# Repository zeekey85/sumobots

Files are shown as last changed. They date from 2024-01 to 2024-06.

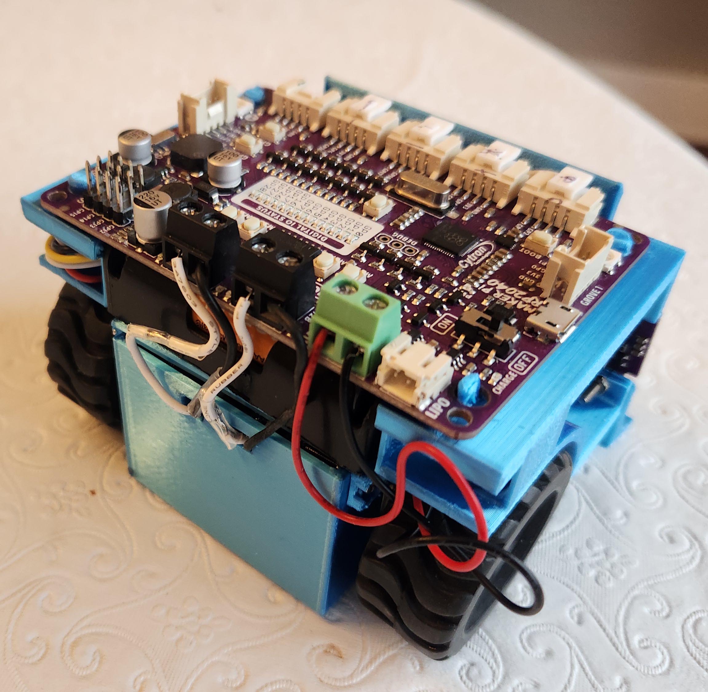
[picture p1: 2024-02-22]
Builders/Bill Ball/Sumo 8/Complete views/sumo 8 back.jpg

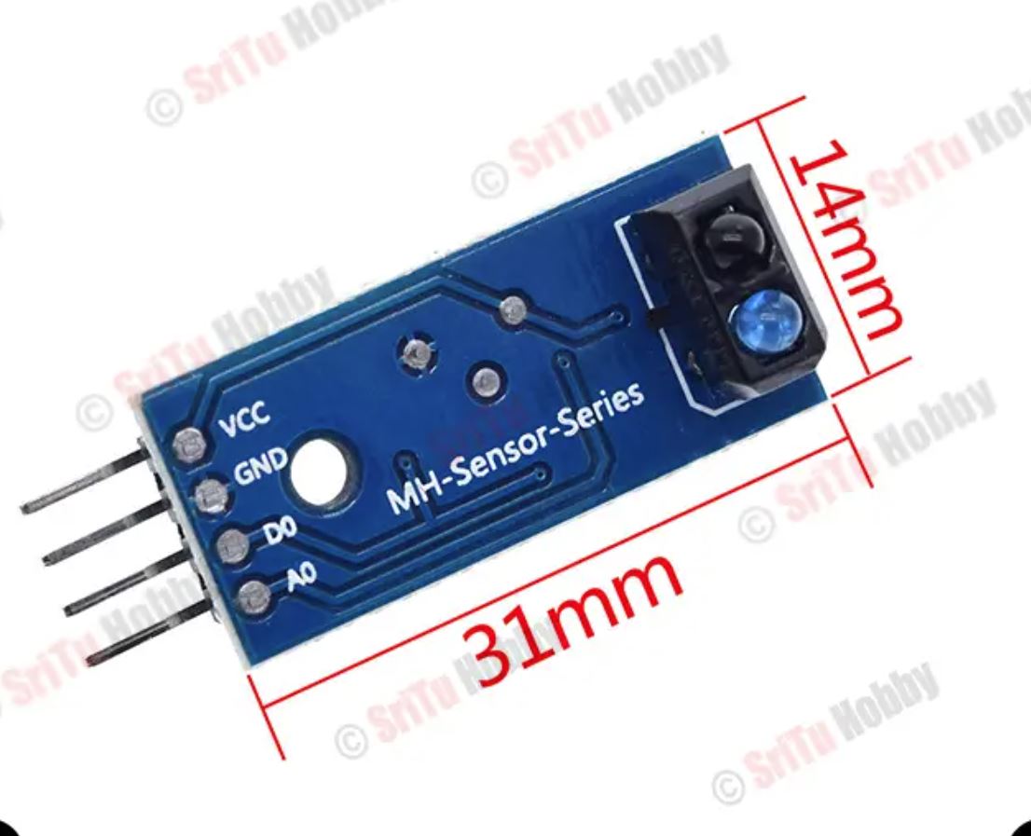
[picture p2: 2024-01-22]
reference/design files/Measurements and images/TCRT5000 measurements.JPG

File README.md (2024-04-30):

# sumobots
A place for development documents and public relases on the mini sumo bot project from It Begins in Brockport.  
Here your will find everything you need to build and compete with your own IBIB2040 class mini sumo bot in the Released folder of this archive.  
General information can be found at https://ibib.us/projects/mini-sumo-robots/  
Contact Bill Ball, bill@tinkerfarm.net with any questions.

Sumo Louis

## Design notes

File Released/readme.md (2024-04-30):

These files are released for public use as a starting point for builds of the IBIB2040 class of Mini Sumo Bots.
A rules document for competition is included.  
An example build is provided in the designs/BB1 folder. This includes a parts list and preparation document, an assembly document, and 3D printable files to create a chassis. A limited number of kits from this build are available.  
Software to be downloaded to the Maker PI2040 board can be found in the code folder.  
General information about the project can be found at https://ibib.us/projects/mini-sumo-robots/  
Send all inquries to Bill at bill@tinkerfarm.net.  

two

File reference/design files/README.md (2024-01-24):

# sumobots
Schematics and datasheets for building and programming IBiB mini sumo bots
Contact Bill Ball, bill@tinkerfarm.net with any questions.

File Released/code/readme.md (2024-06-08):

# Sumo Bot

## Initial setup
Open `settings.py` and review the "Robot hardware settings" section. Change any pin values if your hardware is connected differently than the default settings.

## Installation instructions
Make a backup copy of the code.py file that cam on your MakerPi board.
Copy the files `base-bot.py`, `code.py`, `adafruit_vl53l0x.mpy`, and `settings.py` to your MakerPi to get a working sumo bot.

## How to use
Turn on your MakerPi. To start a bout hold down the GP20 button until the light turns yellow. Your bot is now armed. Release the button to start the bout after a 5 second delay.
See the rules document for more detail on how Sumo bot matches operate.
Turn on your Maker Pi and press buttons until you find the one that turns the lights from red to yellow. Your bot is now armed. Release the button to enter FIGHT MODE!

## How to customize
Change values in the "Settings that control fight mode parameters" section of `settings.py` to make adjustments to your robot's fighting strategy.

## Advanced customization
Modify the `fight()` method in code.py to change your robot's fighting strategy.

## File descriptions 
* `settings.py` contains hardware pin assignments and basic behavior settings
* `code.py` defines the `fight()` method which determines the robot's logic while in fight mode.
* `base_bot.py` contains the main class which defines the fundamental methods for robot control such as moving and detecting enemies.
* `adafruit_Vl530x.mpy` is the driver for the time of flight sensors. The robot code won't work without it installed on the MakerPi.
* `original_code.py` is the default demo program that shipped with the MakerPI RP2040. It's not needed for the robot to work.

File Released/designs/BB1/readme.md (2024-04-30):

This is the complete plans for a mini sumo robot that conforms to IBiB2040 rules and is based around the Maker Pi RP2040 robotics board. It also comples with the generally used mini sumo rules.

An illustrated complete parts list is included in the "parts preparation.pdf" document.

Stl files for 3D printing the four body parts are included.

Illustrated assembly instructions can be found in the "assembly instructions.pdf" file.

The Maker Pi board should be running CircuitPython (it ships this way) and will need the code files in the code folder copied to it.

All material in this archive except the adafruit_vl53l0x.py file is CC0 "no rights reserved." adafruit_vl53l0x.py has a MIT license.  
Send any questions to: bill@tinkerfam.net

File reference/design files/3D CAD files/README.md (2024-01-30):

# sumobots
CAD files to be used to design IBiB mini sumo bots.
Contact Bill Ball, bill@tinkerfarm.net with any questions.

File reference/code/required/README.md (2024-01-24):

# sumobots
Reference code to include in sumo bots.

original code.py is the defaut code shipped on Maker pi boards. It should be included on all sumo boards.

adafruit_vl530x.mpy is the driver for the ranging sensors. It should be included in the lib folder of all sumo boards.

The Adafruit repository for CircuitPython on the maker pi board is here: https://circuitpython.org/board/cytron_maker_pi_rp2040/
The board ships with CircuitPython 7.1.0

Contact Bill Ball, bill@tinkerfarm.net with any questions.

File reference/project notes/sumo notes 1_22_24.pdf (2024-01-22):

IBiB Mini Sumo project notes. 1/21/2024. Bill Ball

The bots will meet standard specifications: 10cm x 10cm x unlimited, 500 grams max.

The bots will have the following components:

1. 4xaa battery holder. $0.5-$1. Is the 1x4 or 2x2 layout better? Builders supply their own batteries.

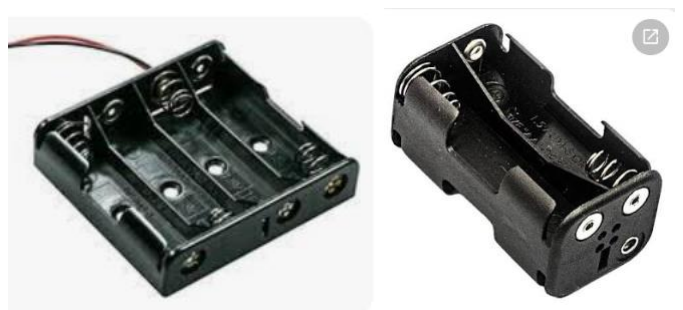
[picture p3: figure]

2. Maker Pi RP2040 main board with OEM Circuitpython 7 and accompanying 4 x grove to header pin wire sets. Cheapest source in bulk @$10: Newark. Manufacturer reference: https://www.cytron.io/p-maker-pi-rp2040-simplifying-robotics-with-raspberry-pi-rp2040 (https://www.cytron.io/p-maker-pi-rp2040-simplifying-robotics-with-raspberry-pi-rp2040)

The adafruit_vl5310x.mpy library will be installed by us. The default code.py will be renamed and a basic sumo bot program will be added as code.py.

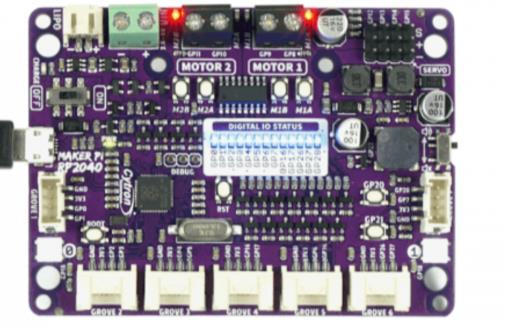
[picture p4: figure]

3. N20 6V motors (2). What rpm/torque trade off is best? We will start at 150rpm. $4.20 per pair from Aliexpress. We will need to solder on leads. Mounting brackets will be 3D printed (standard ones are too short for the wheels).

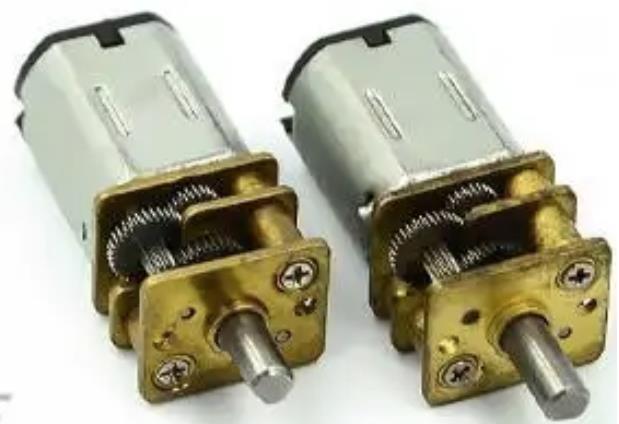
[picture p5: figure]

### 4. K346 43*19*3mm D-hole Rubber Wheel (2). $1.5 per pair from Aliexpress

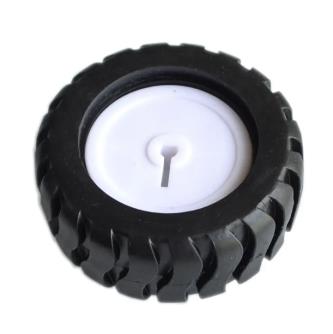
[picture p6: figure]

5. VL53L0X Time-of-Flight Ranging Sensor (2). $2.60 per pair from Aliexpress. We will need solder the header pins. We will use the VCC, GND, SCL, SDA, and XSHUT pins. XSHUT is required to change the I2C address in software. We are not planning to use the GPI01 (data ready) pin (it would require an additional grove wire set if we do). If two sensors doesn’t work well we may need to go to three, which would require 2 additional grove wire sets and may not all fit on the same I2C bus as exposed by the Maker pi.

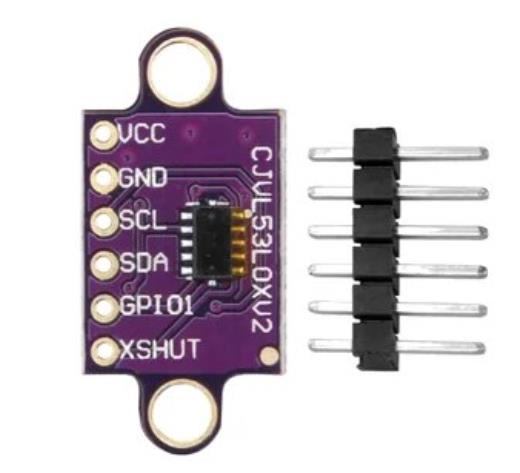
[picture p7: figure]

6. TCRT5000 Infrared Reflective Sensor Module (2). $1.5 per pair from Aliexpress.

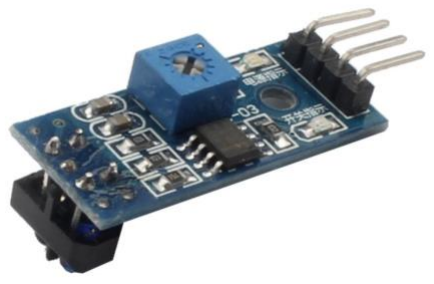
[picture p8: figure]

7. USB A to micro USB cable for programing. We may want to offer other formats to micro options. $1 from Aliexpress. People don’t otherwise acquire micro USB cables anymore.
8. Chassis. etc. The chassis can be user designed/built. We will need to develop a design for 3D printing, maybe laser cut or even milled. We also need to decide on ballast and fasteners. The basic bot only weighs about 250 grams. We should supply enough repositionable ballast to reach 500 grams. I use steel BBs but they need to be contained. We can do this project with m2 Philips head fasteners throughout. It would be incredibly kind to builders if fasteners are all the same length. 14mm? As a supplied kit let’s plan on $5 total cost of supplies.

Total delivered cost is currently about $27 for supplies when items are purchase qty 10 or greater using mostly Aliexpress.

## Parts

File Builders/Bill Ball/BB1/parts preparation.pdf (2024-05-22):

Parts preparation information for the Mini Sumo BB1 robot.

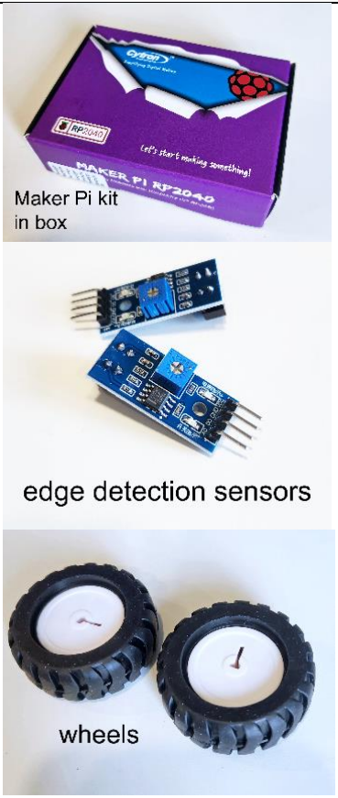
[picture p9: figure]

1. The parts list for the robot:

A Maker Pi RP2040 kit in box. The box includes one Maker Pi board, 4 Grove connector to female header pin cables, a mini screwdriver, and 4 adhesive feet. The feet are not used in this project.

Two ToF (VL53L0X Time of Flight) sensors of the type pictured in this document.

Two edge detection (TCRT5000 infrared reflective) sensors of the type pictured in this document (with right angle header pins, sensor and adjustment screw on opposite sides).

Two N20 6 volt gear head motors, low torque models only. 150 or 200 rpm motors suggested.

Wire and heat shrink for motor leads if they are not pre-soldered to the motors.

Two 43mm x 19mm treaded tires mounted on 3mm D shaft wheels, as shown.

One 4 x AA battery holder of the type pictured in this document, along with 4 AA batteries.

A minimum of eight m3 x 10mm pan head screws (referred to as bolts in the documentation).

One m3 x 10mm countersunk screw (referred to as bolts in the documentation).

A minimum of 9 nuts for the m3 bolts.

Four 3D printed parts.

Ballast weight as desired. About 200 grams of Steel BBs are suggested.

A Phillips screwdriver.

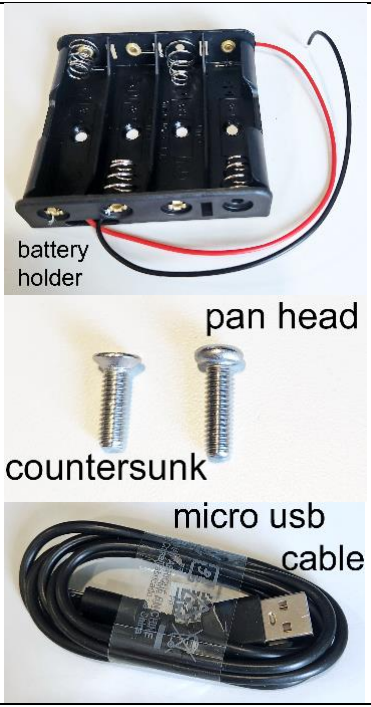
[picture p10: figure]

Small needle-nosed pliers.

A micro USB cable for programming, along with downloaded software.

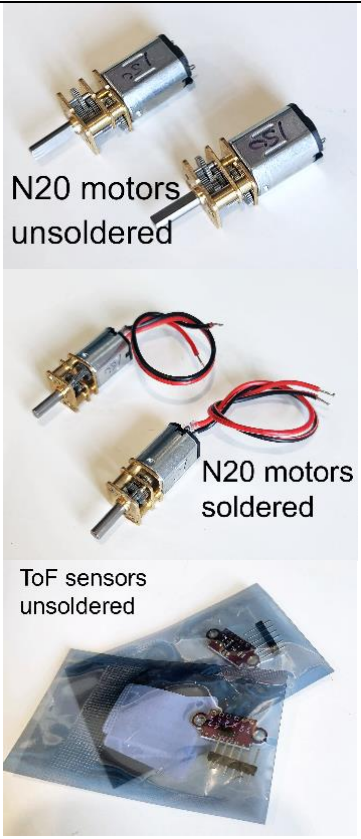
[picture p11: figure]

2. If the motor wires are not soldered to the motors and this exposed wire at the connection covered with heat shrink, this will need to be done with two pairs of wire, about 80mm long.

The edge detection sensors usually ship with right angle header pins already soldered on and in anti-static bags. They do not need further preparation.

The ToF sensors usually ship unsoldered with header pins included in the anti-static bag.

The yellow protective film covering the black rectangle on the ToF sensors will need to be removed if it has not already been done.

If the ToF sensors have not had their header pins soldered on, this will need to be done. The longer pins are in the back of the sensor and it is soldered from the front.

3. The four 3D printed parts: main body, fender bar, lid, and blade can be printed with standard settings. Printing time varies widely but plan on 8 hours of print time total.

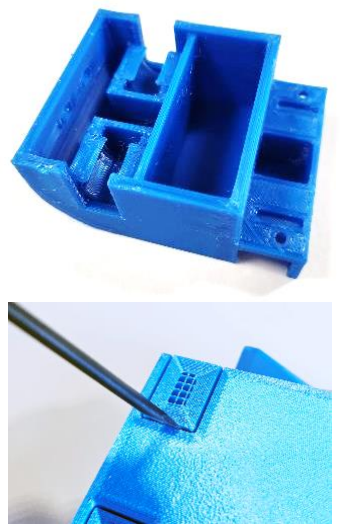
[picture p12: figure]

Only the main body needs to be printed with supports. The body is printed upright on the printer bed, as shown. Once it is off the printer the supports can be removed by popping them off the side of the body and at the curved rear from underneath. The supports interface to the main body does not need to be cleaned up fully, although the bolt holes should be cleared.

The fender bar is printed “face” down on the bed, as shown.

The lid should be printed upside down on the bed, as shown, with the flat side on the bed.

The blade is printed with its back (the flattest part) on the bed, as shown. It does not need supports.

Some holes may need to be cleared with a 3mm drill bit to accommodate bolts without breaking the part.

Parts preparation is complete and assembly can begin.

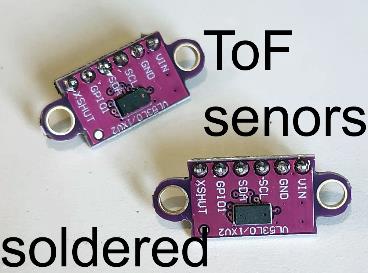
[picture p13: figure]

# Main Body

# Fender Bar

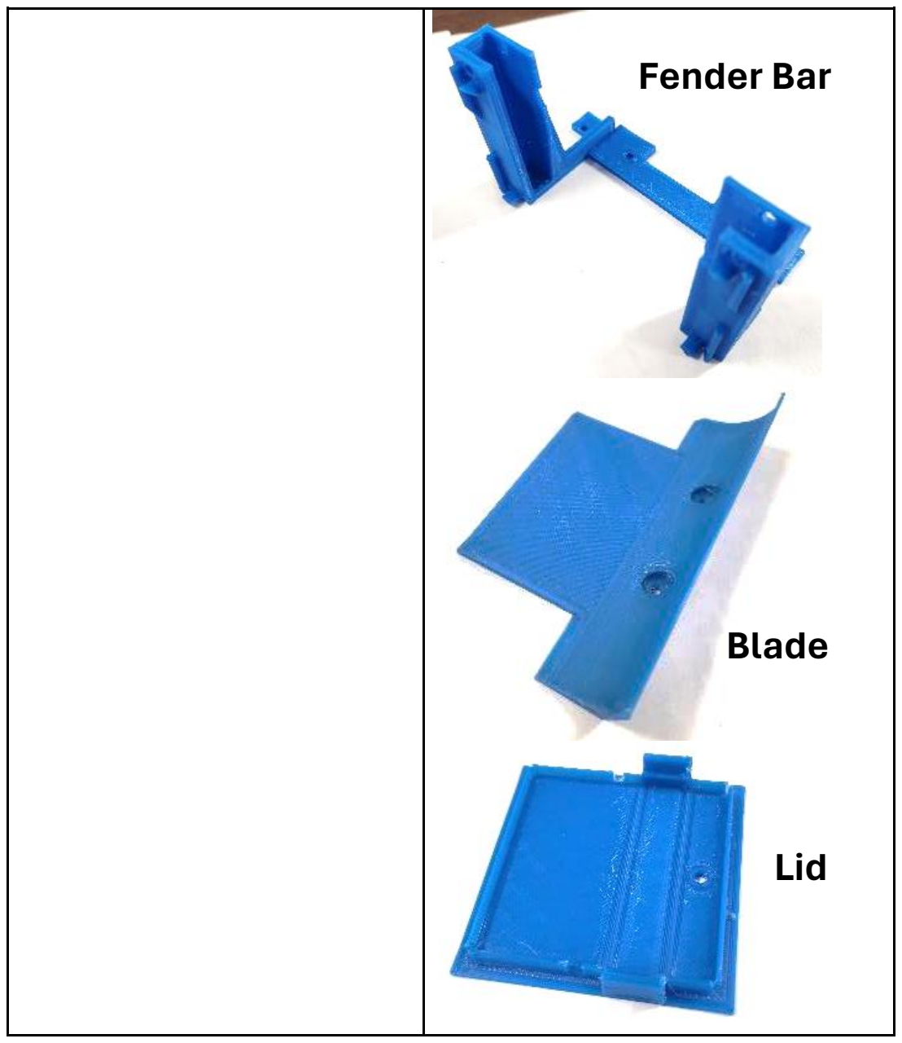
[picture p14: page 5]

# Blade

# Lid

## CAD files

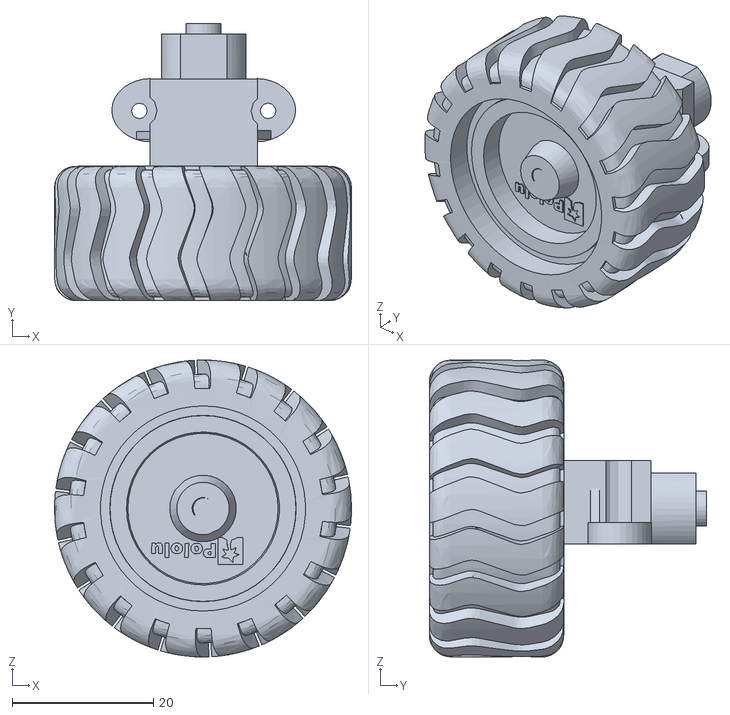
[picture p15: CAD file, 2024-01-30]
reference/design files/3D CAD files/wheelmotormount assembly.stl
42.0 x 39.2 x 42.0

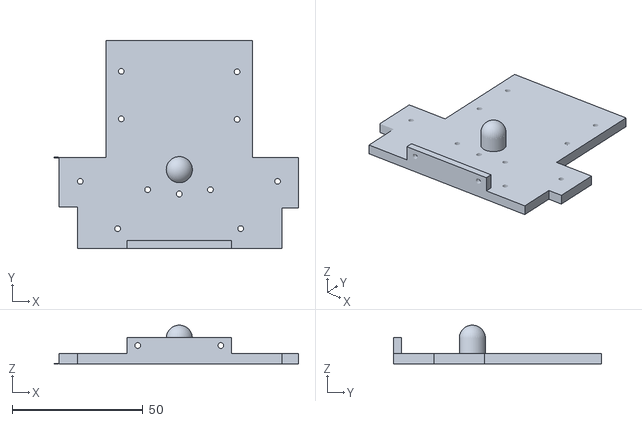
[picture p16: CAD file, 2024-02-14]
Builders/Bill Ball/Sumo 4/Files for 3D printing/main plate.stl
93.3 x 79.6 x 14.8

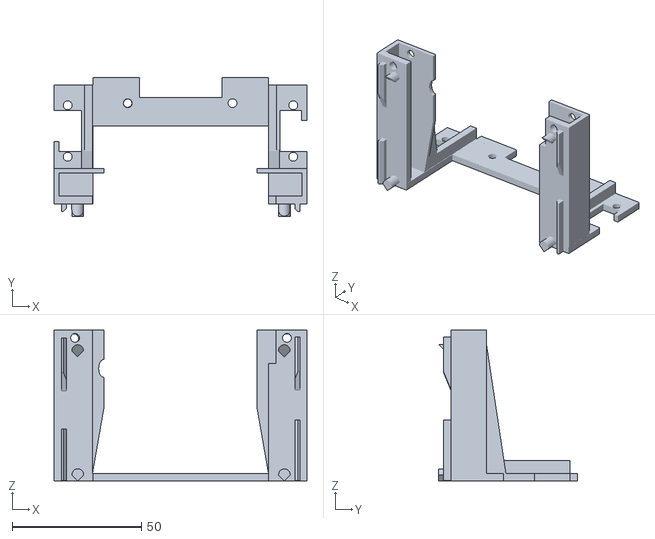
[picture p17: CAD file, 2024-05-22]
Builders/Bill Ball/BB1/Sumo BB1 fender bar.stl
97.9 x 53.9 x 58.4

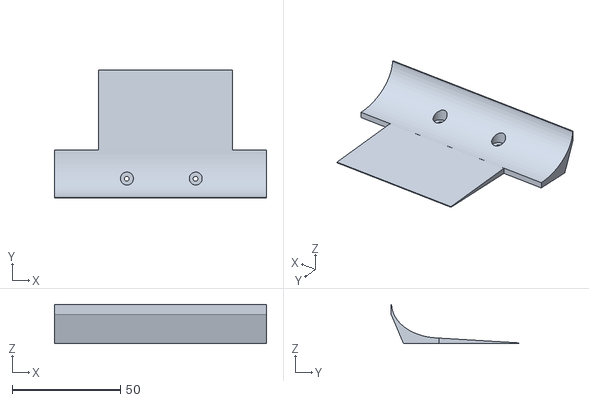
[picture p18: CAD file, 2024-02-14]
Builders/Bill Ball/Sumo 4/Files for 3D printing/blade.stl
98.0 x 59.0 x 18.1

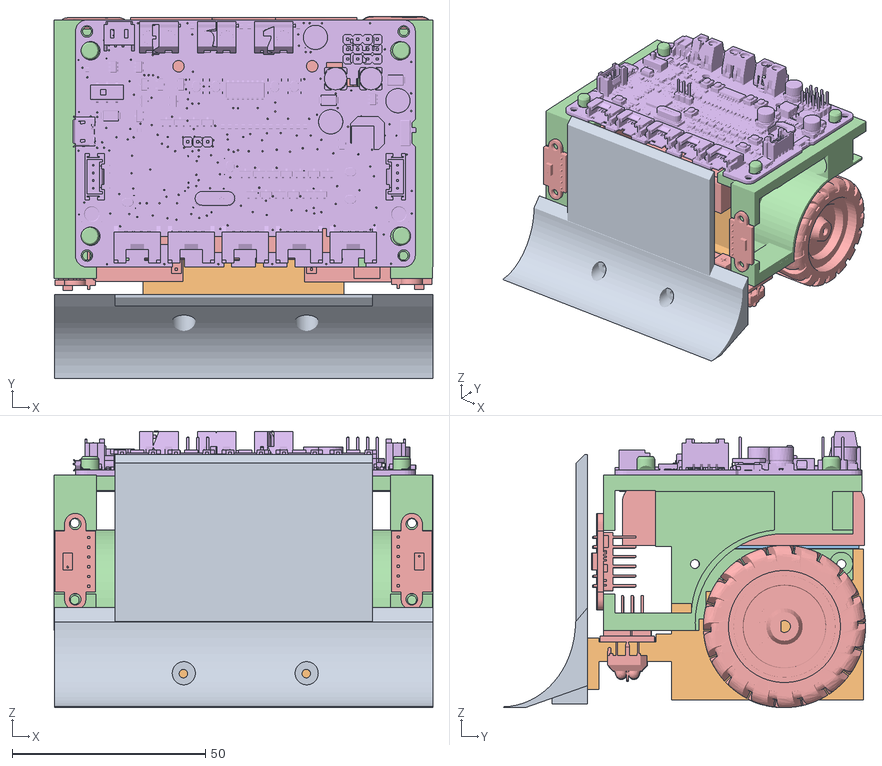
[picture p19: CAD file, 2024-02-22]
Builders/Bill Ball/Sumo 8/Complete views/tinker.obj
98.1 x 93.7 x 71.5

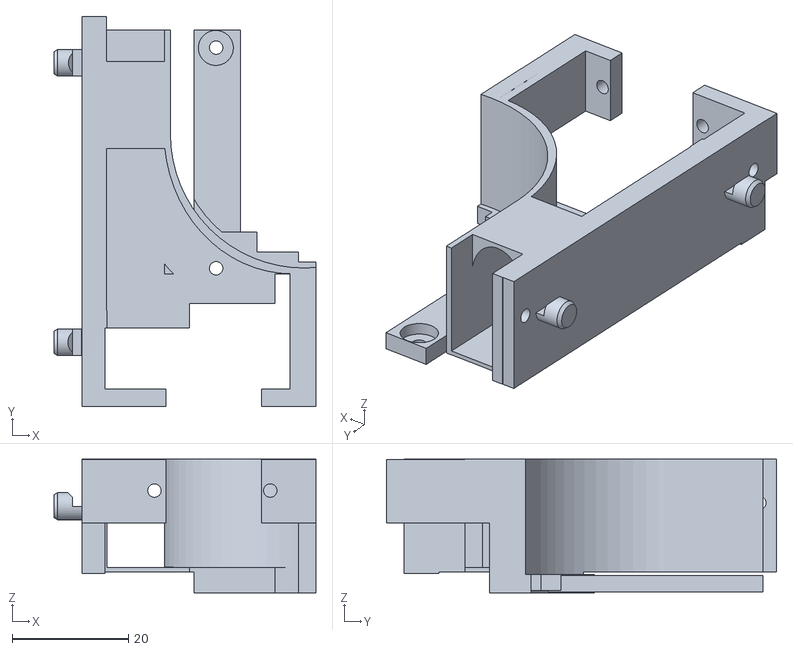
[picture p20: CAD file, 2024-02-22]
Builders/Bill Ball/Sumo 8/Parts/sumo 8 left fender.stl
45.0 x 67.0 x 22.9

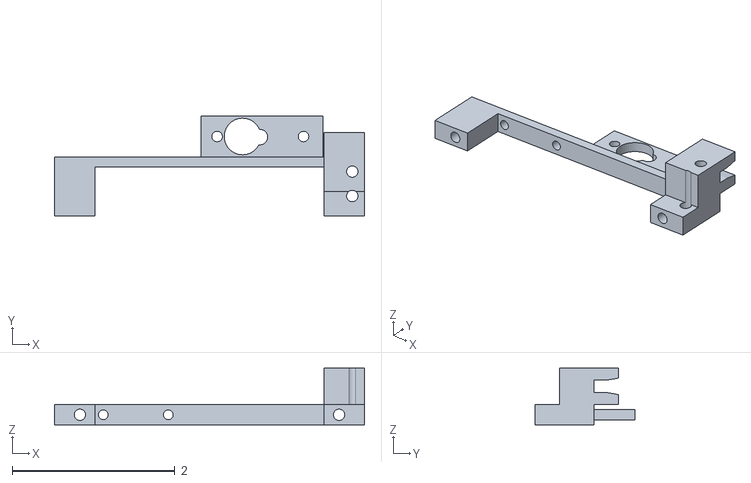
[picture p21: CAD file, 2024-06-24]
SumoBot Accessory Holder v1 v3.stl
3.81 x 1.23 x 0.7

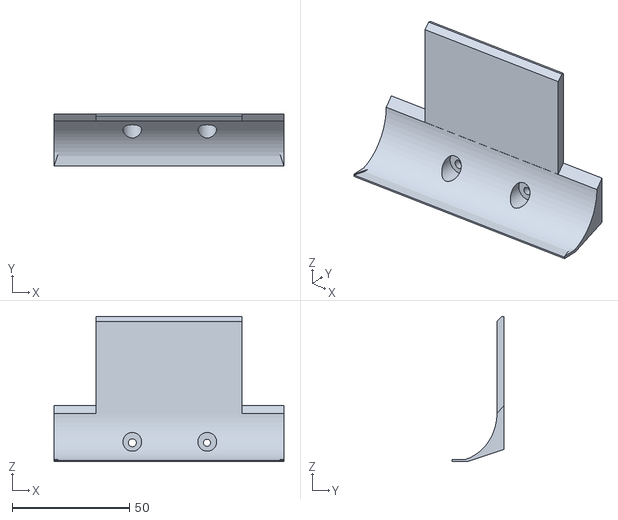
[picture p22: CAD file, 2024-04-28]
Builders/Bill Ball/BB1/Sumo BB1 blade.stl
98.0 x 22.2 x 62.0

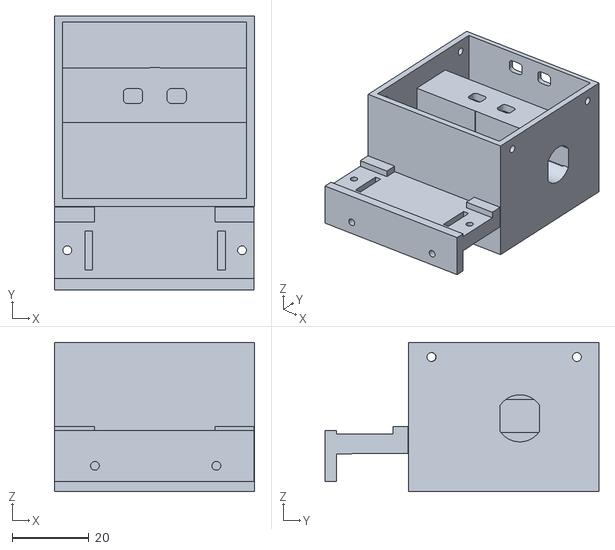
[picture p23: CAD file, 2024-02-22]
Builders/Bill Ball/Sumo 8/Parts/sumo 8 body.stl
52.2 x 71.5 x 39.0

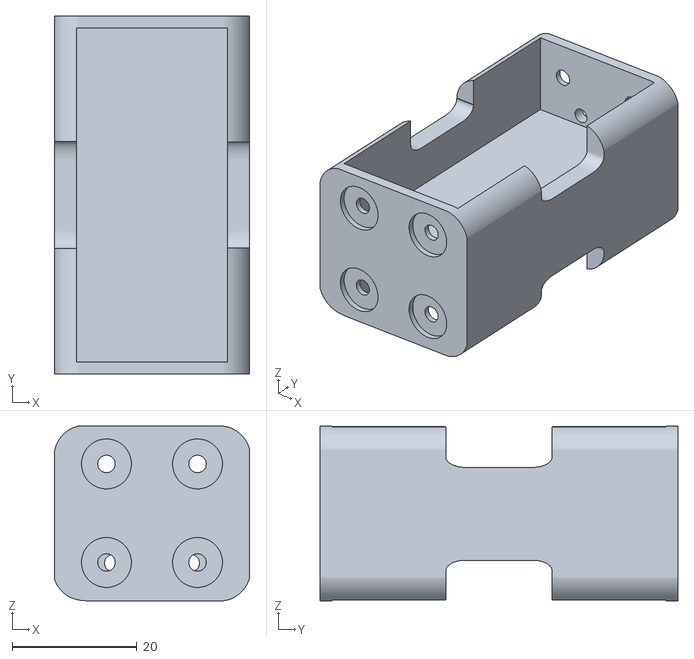
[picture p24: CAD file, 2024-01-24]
reference/design files/3D CAD files/2x2 AA battery holder.stl
31.3 x 57.4 x 28.0

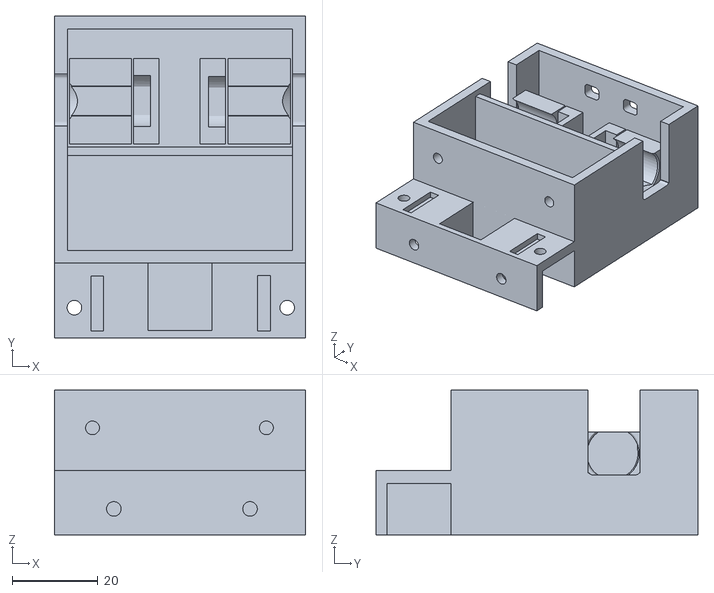
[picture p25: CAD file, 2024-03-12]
Builders/Bill Ball/BB1/Sumo BB1 body.stl
58.6 x 75.2 x 33.8

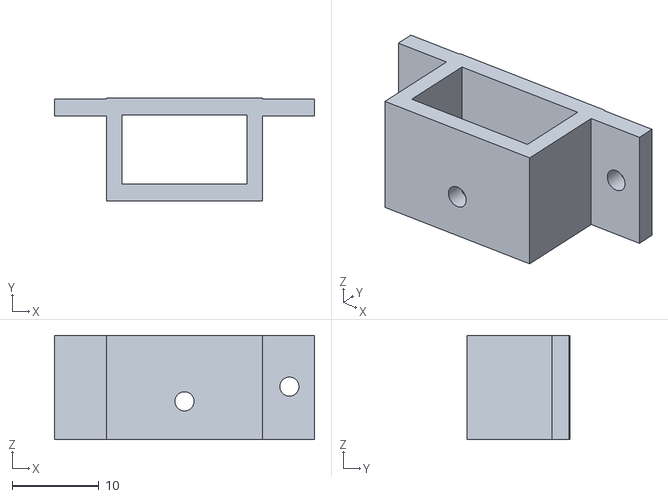
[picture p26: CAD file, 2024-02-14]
Builders/Bill Ball/Sumo 4/Files for 3D printing/battery holder bridge.stl
30.0 x 11.9 x 12.0

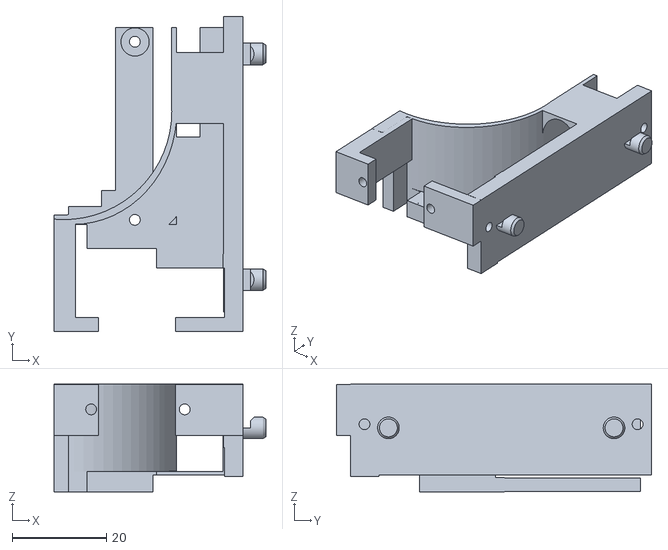
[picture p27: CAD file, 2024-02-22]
Builders/Bill Ball/Sumo 8/Parts/sumo 8 right fender.stl
45.0 x 67.0 x 22.9

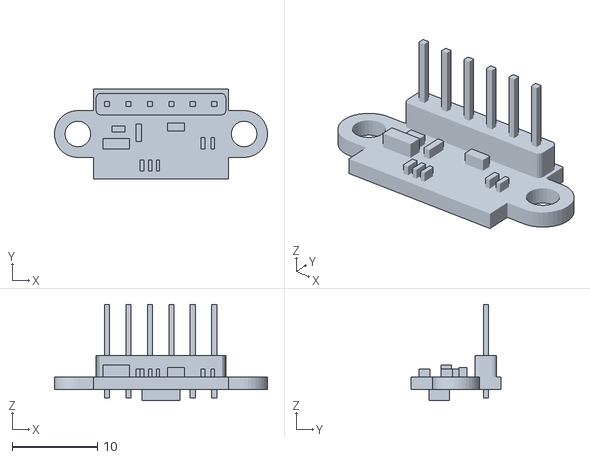
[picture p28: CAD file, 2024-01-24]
reference/design files/3D CAD files/VL53L0X TOF Sensor.stl
25.0 x 10.5 x 11.3

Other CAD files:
Released/designs/BB1/Sumo BB1 body.stl
Builders/Bill Ball/Sumo 4/Files for 3D printing/left fender.stl
Builders/Bill Ball/Sumo 4/Files for 3D printing/right fender.stl
Builders/Bill Ball/Sumo 8/Parts/sumo 8 blade.stl
Builders/Bill Ball/Sumo 8/Parts/sumo 8 cover.stl
Released/designs/BB1/Sumo BB1 lid.stl
reference/design files/3D CAD files/1x4 AA battery holder.stl
reference/design files/3D CAD files/K345-wheel-42x19mm lowres.stl
reference/design files/3D CAD files/K346-wheel-42x19mm.f3d
reference/design files/3D CAD files/MAKER-PI-RP2040 lowres.stl
reference/design files/3D CAD files/MAKER-PI-RP2040.f3d
reference/design files/3D CAD files/N20_gear_motor.stl
reference/design files/3D CAD files/TCRT5000 sensor.stl
reference/design files/3D CAD files/n20_motor_mount.stl

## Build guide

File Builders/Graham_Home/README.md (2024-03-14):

## How to use this code:
1. Copy the folder "adafruit bus device" and the file "adafruit_vl53l0x.mpy" from the [Adafruit CircuitPython Bundle](https://circuitpython.org/libraries) to the "lib" folder on your MakerPi.
2. Copy all .py files from the code/ directory to your MakerPi.
3. MakerPi NeoPixels will light up red. Hold the GP20 button and release it (NeoPixels will turn yellow when button is held and green when button is released).
4. You are now in sumo mode! Robot will seek out an opponent and attempt to shove it out of the ring. 

You can run `copy-code.ps1` on a Windows computer to copy the code files to your MakerPi, just remember to update 
the `copy-code.ps1` script with the correct path to the code directory and the correct drive letter for the MakerPi.

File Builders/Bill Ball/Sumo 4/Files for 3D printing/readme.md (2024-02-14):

This a first chassis for testing purposes. It doesn't leave much room for ballasting.
See https://www.tinkercad.com/things/8du6Ch6ZOo7-public-sumo-bot-4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 for assembly tips.

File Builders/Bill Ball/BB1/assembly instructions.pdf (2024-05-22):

Assembly instructions for BB1 mini sumo bot. Please consult the parts preparation information before assembly.

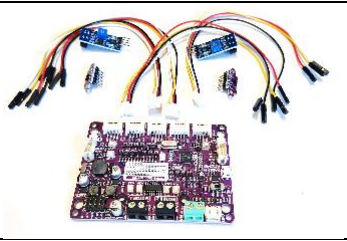
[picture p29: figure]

1. Lay out the electronics for the robot. This
includes the Maker Pi RP2040 board (qty. 1) with grove connecter cables (qty. 4), ToF (VL53L0X Time of Flight) sensors (qty. 2), and edge detection (TCRT5000 infrared reflective) sensors (qty. 2).

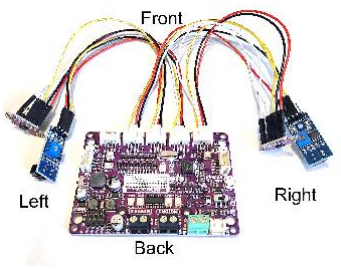
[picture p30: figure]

2. Connect the electronics according to the following list, using the labels on the parts. The Grove port numbers and pins are listed on both the top and the bottom of the Maker Pi board. All sensors have connection labels on them. Note that all references to “le ft,” “right,” etc. in these instructions refer to the robot’s point of view.

Grove 2
GND -> Right ToF GND
3V3 -> Right ToF VIN
GP2 -> Right ToF SDA
GP3 -> Right ToF SCL

Grove 3
GND -> Left edge detection GND 3V3 -> Left edge detection VIN GP4 -> Left ToF XSHUT
GP5 -> Left edge detection DO

Grove 4
GND -> Left ToF GND
3V3 -> Left ToF VCC
GP16 -> Left ToF SDA
GP17 -> Left ToF SCL

Grove 5
GND -> Right edge detection GND 3V3 -> Right edge detection VCC GP6 -> Right ToF XSHUT

GP26 -> Right edge detection DO

Set the electronics assembly aside while keeping track of the left/right orientation of parts. It’s a good idea to mark L or R on the sensors with a sharpie.

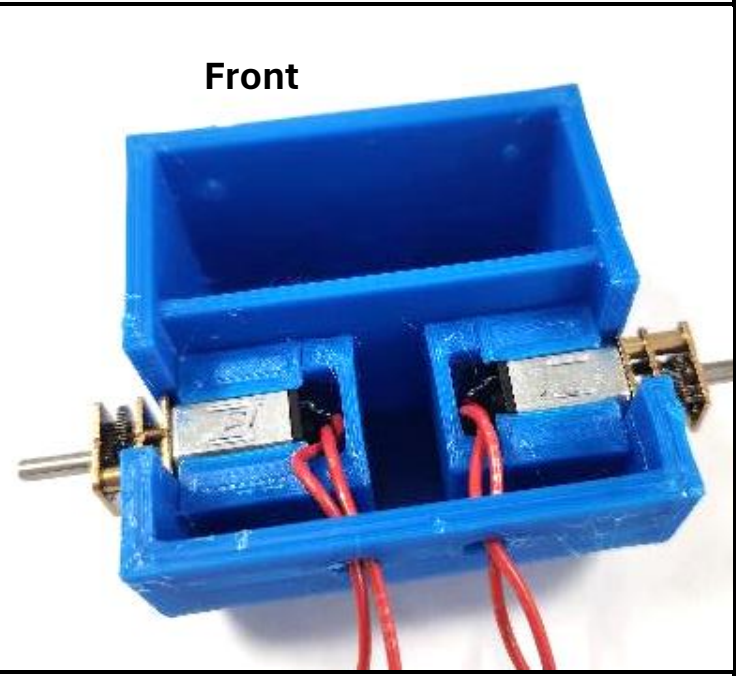
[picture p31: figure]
Front

3. Insert the motors into the main body. It doesn’t matter which motor goes into which side.

The motors are held in the robot by friction, and it may require some pressure to insert them fully. Hold them by the brass plates on their gearbox while inserting. Ideally the brass plate closest to the silver motor housing should align with the inside of the main body wall, as illustrated. However, as long as it aligns with the outside of the wall installation will be adequate. Forcing the installation could crack the main body. Thread the motor wires up and out of the main body through the supplied holes at the back of the body.

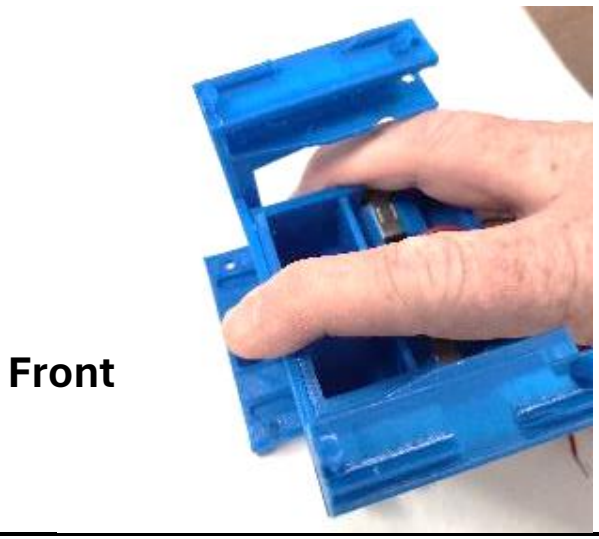
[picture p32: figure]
Front

4. Install the fender bar onto the main body with two bolts inserted from the front and secured with nuts from inside the front wall of the main body.

Note that the fender bar is easily bent in some directions and applying pressure in those directions can warp or even break it. Do not squeeze or twist the bar or put pressure on it from the top. Instead always hold it flat against the main body while installing and put any pressure on the main body.

5. If the front ballast box is being used, fill the box and secure the ballast. BBs will get loose and roll all over. These should be mixed with some sort of glue and poured in if used (not illustrated). Allow the glue to set before proceeding.

Install the edge detectors to the main body by bolting them down from the top and securing them underneath with nuts. Bolt the left sensor (attached to Grove port 3) to the left side of the robot and the right sensor to the right side. The blue adjustment screw blocks on the sensors point upward, and one block sits closer to the main body than the other.

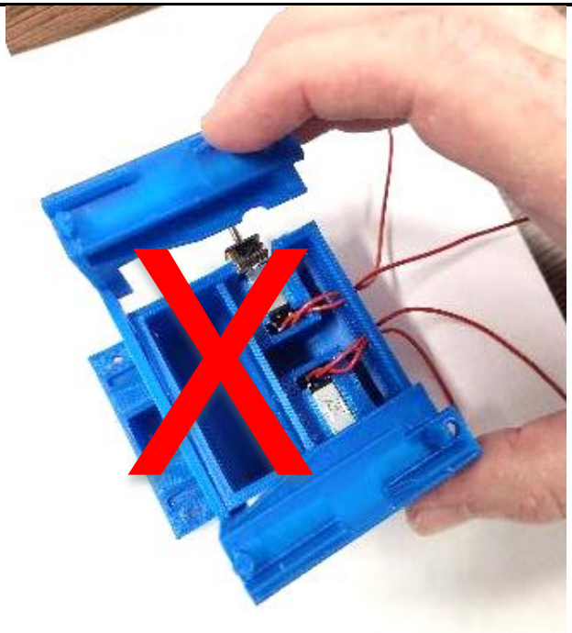
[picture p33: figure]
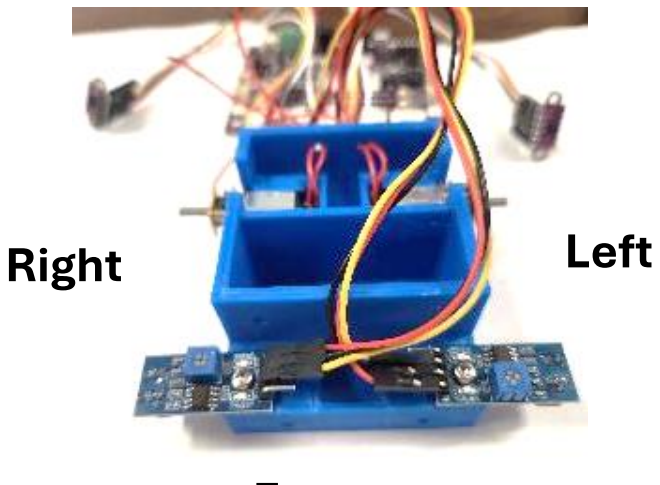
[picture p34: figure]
Right; Left

## Front

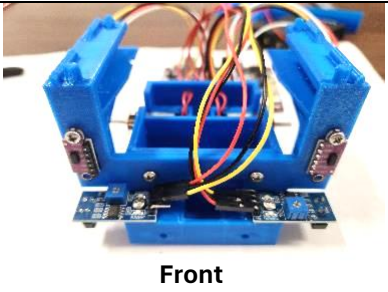
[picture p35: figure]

6. Insert and mount the ToF sensors. Insert the correct sensor into the correct side of the body. The left sensor is attached to Grove port 4 for VCC and GND. Secure the sensors with a bolt at the top of each sensor and a nut inside the top hole on the fender bar. The bottom of the sensor does not need a bolt (the bottom holes are there to be used in case the top ones break out). Note that the black rectangles on the sensors are at the outside edges of the robot. | Front

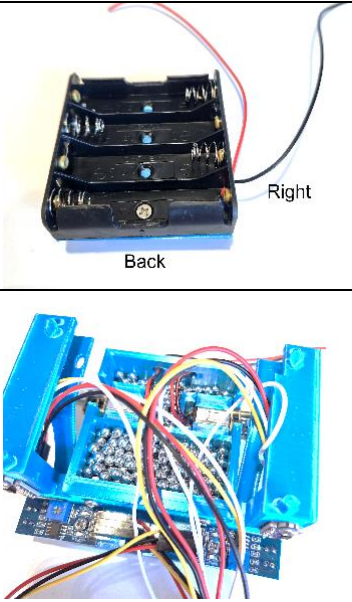
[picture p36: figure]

7. Mount the battery box to the flat side of the lid using the countersunk bolt. Bolt from the inside of the battery box through the box and lid and secure underneath with a nut. The top of the bolt should not be above the top of the inside of the battery holder bottom so that the batteries will install fully. The battery wires should be on the right side of the assembly with the bolt in the rear hole in the box, as shown.
8. If the main body will be ballasted, fill one or both compartments with ballast. If the ballast is electronically conductive is important that the ballast cannot come into contact with the soldered tabs at the back of the motors. Here steel BBs are being used (on an older chassis design), but they are too large to come into contact with the motor tabs.

Round ballast can easily roll out of the ballast box and spill widely until secured with glue and the glue has set. It’s important to weigh all of your robot’s components together before the glue has set to make sure your robot will not exceed 500 grams.

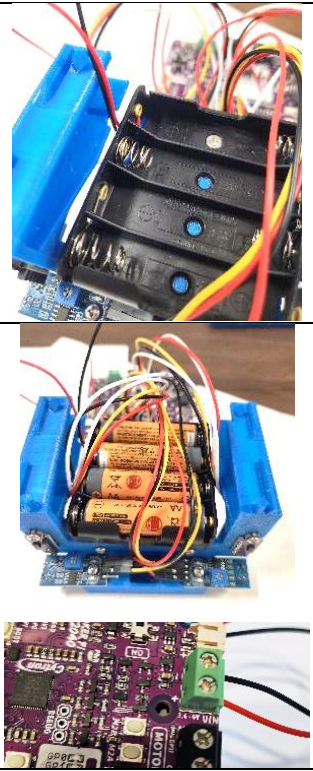
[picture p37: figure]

9. Add the lid/battery box assembly to the main body. It should snap into place on all four sides. There is a notch in the fender bar that will allow the battery wires to come up into it.
10. Install the batteries in the orientation shown on the battery box.

Be aware that the battery wires are now live (there is no on/off switch on the battery box) and the exposed ends can give a shocking lesson in how many watts 4 AA batteries can produce. Do not let the exposed ends of the battery wires contact each other or short against anything conductive. It’s a good idea screw them down to the green terminal block on the Maker Pi board right away. The screws on the block open to provide a clamp to secure the wires when closed. Make sure the black battery wire is secured to the clamp marked “-” on the front of the block and the red wire to the clamp marked “+” to have the correct polarity. The exposed wire (but not the insulated part) should be fully enclosed by the terminal block clamps.

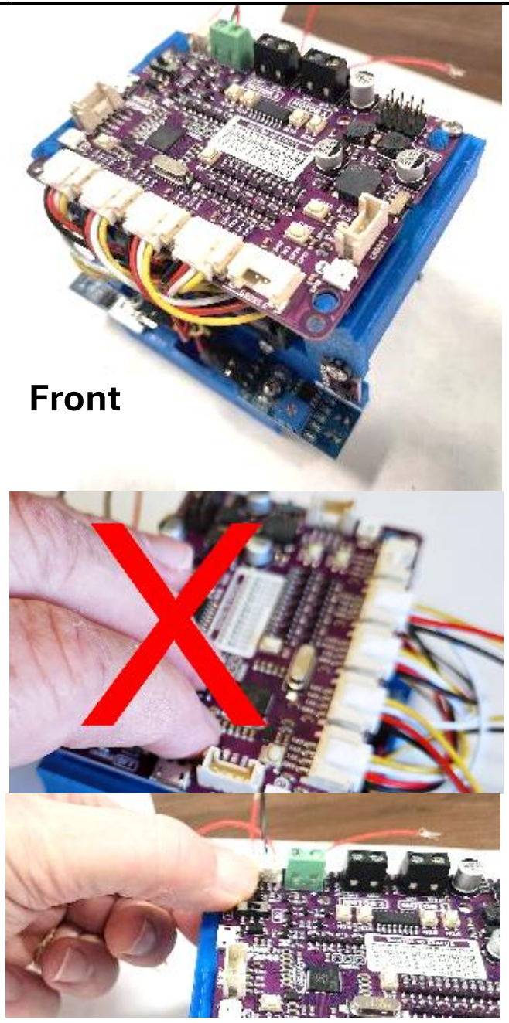
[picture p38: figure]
Front

11. The extra wiring can be rolled into loops and placed between the top of the battery holder and the top of the fender bar. Loose wire should not be left where the wheels will go.

The Maker Pi board can be snapped into place over the posts in the fender bar. The white grove connectors go at the front.

Do not attempt to snap the Pi board down by pressing down from above. This will permanently warp or possibly break the fender bar.

Instead, snap the front of the board into the posts at the front of the robot by squeezing the board and the top layer of the fender together on both sides. It may be difficult the first time it is done. Then snap the board to the rear posts on both sides by squeezing the board and the top layer of the fender together at the back, as shown.

The board can be bolted down to the fender bar using the holes at the back.

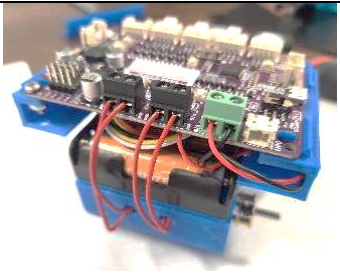
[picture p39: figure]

12. Screw the exposed ends of the motor wires to the black “Motor 1” terminal (for the left motor) and the “Motor 2” terminal (for the right motor) on the battery board. At this point it doesn’t matter which wire goes to which clamp on the terminal as motors do not have polarity and these wires can easily be reversed if you find your robot goes backwards when you want it to go forward.

Tuck in the wiring by pushing the battery wires into the right fender channel and pushing the motor wires into the main body. The extra length will be needed later to change batteries without unscrewing the wires.

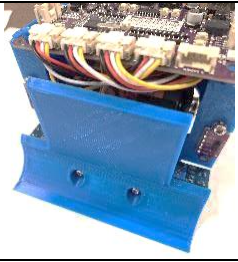
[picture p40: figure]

13. Attach the front blade to its mount on the main body by inserting two bolts from the front for the blade and securing them with nuts underneath. The front of the blade will be slightly lower than the main body. The robot will sit level once the wheels are attached.

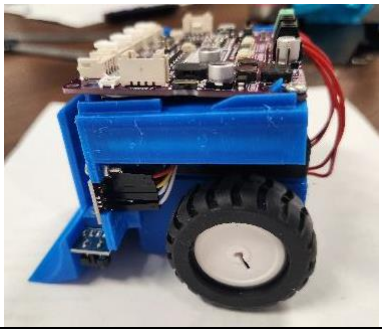
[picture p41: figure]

14. Mount the wheels and tires with the flatter side of the wheel to the outside. The motor shafts have a D shape and this should be aligned the D shape on the wheel before they are pressed on. They should be against the main body without being so tight against it that they cause friction.

Note how the wires from the ToF sensors are pulled up into the fender bar so they don’t rub on the wheels.

Assembly is complete. Now is a good time to make sure your robot will fit with the regulation width of 10 cm and length of 10 cm (loosely fitted wheels and wires may cause it to be oversized).

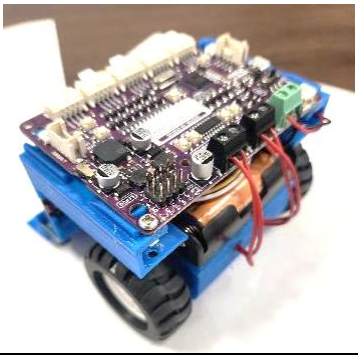
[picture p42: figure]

15. If software has not been downloaded it can be done now.

The Maker Pi board has to be turned on to download software or run the robot.

When it is time to change the batteries you can do so without tools. Pull the extra wire from batteries and the motors out from storage and spread them apart enough to clear the battery box. Gently lift the battery off the main body and slide it out of the back of the robot to replace the batteries.

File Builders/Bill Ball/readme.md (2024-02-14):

Design files from Bill Ball. Feel free to use. Send any questions to:
bill@tinkerfam.net

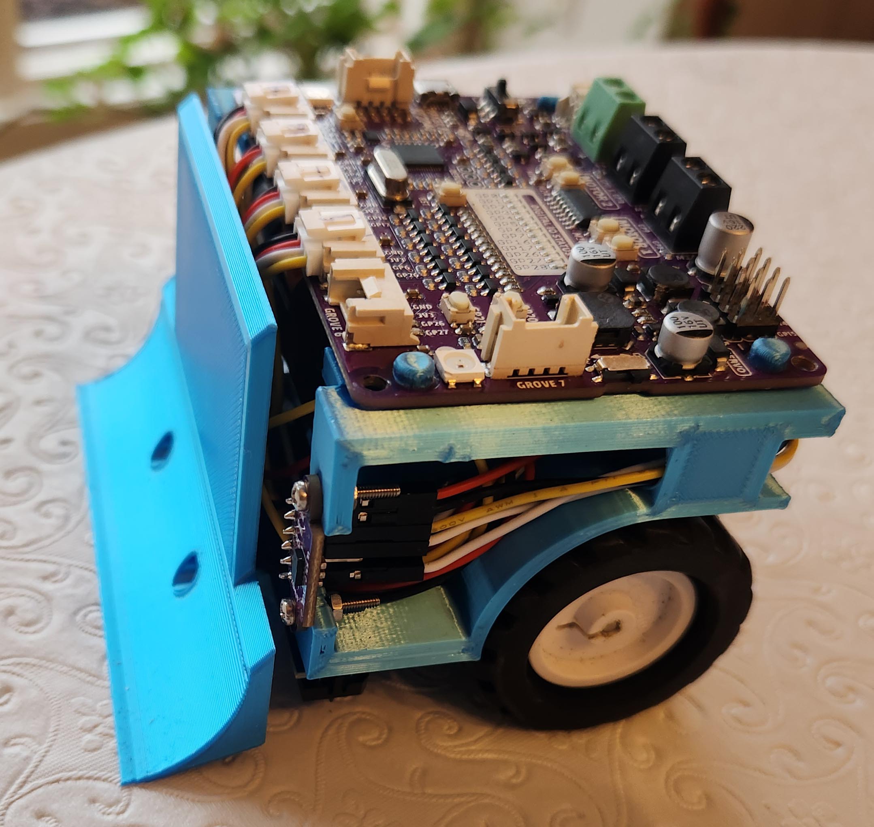
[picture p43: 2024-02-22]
Builders/Bill Ball/Sumo 8/Complete views/sumo 8 front.jpg

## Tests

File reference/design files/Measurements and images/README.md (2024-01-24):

# sumobots
Measurements and images of components for IBiB mini sumo bot.
This is to accompany CAD files.
Note that some commodity parts (i.e. battery holders) may vary slightly in dimensions.
Contact Bill Ball, bill@tinkerfarm.net with any questions.

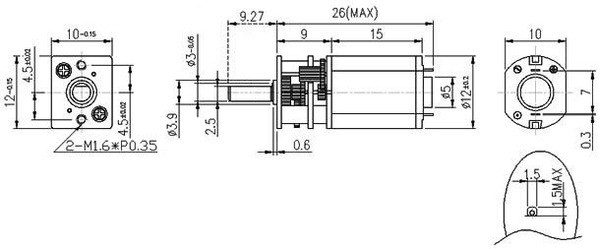
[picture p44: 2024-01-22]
reference/design files/Measurements and images/N20 motor measurements.jpg

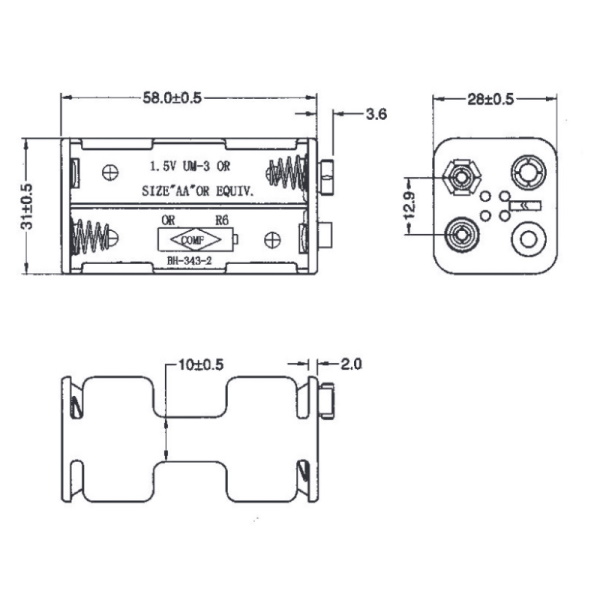
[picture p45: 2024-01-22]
reference/design files/Measurements and images/2x2-4AA battery-holder-dimensions.jpg

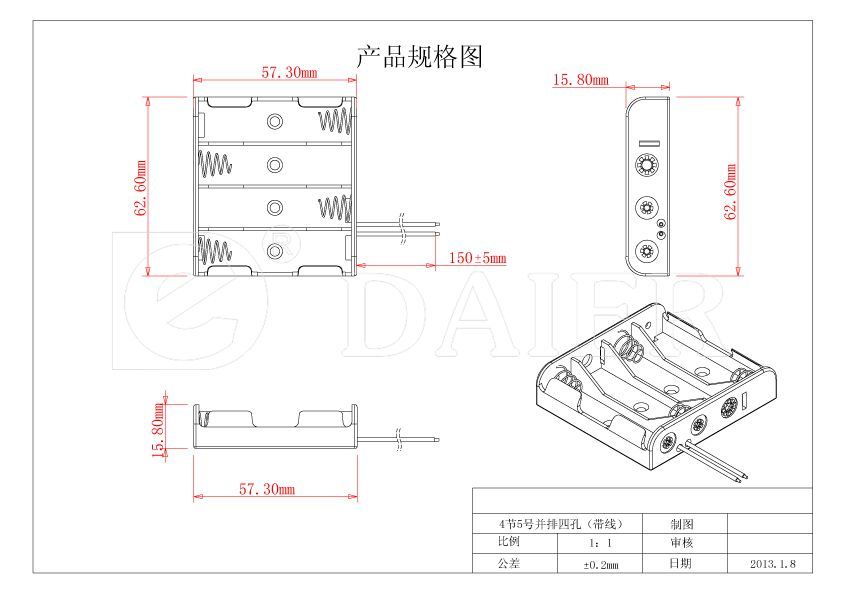
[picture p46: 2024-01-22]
reference/design files/Measurements and images/1x4-4AA-6V-Battery-Holder dimensions.jpg

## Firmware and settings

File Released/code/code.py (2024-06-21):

import random
import time
from time import sleep

from base_bot import SumoBotBase
from settings import *

#Just figuring this github stuff out
class SimpleSumoBot(SumoBotBase):
    """
    An implementation of the sumo bot fighting routine.
    Other botmasters may define their own SumoBot classes which extend SumoBotBase,
    and add their own fight() method with their own personal fighting strategy.
    """

    def fight(self):
        """
        Robot fighting routine.
        """
        # *************************************
        # 1. Back away from the edge if needed
        # *************************************

        # If both sensors are over the edge, drive straight backwards.
        if self.left_edge_detected() and self.right_edge_detected():
            print("Backing straight up and turning around")
            self.drive(left_speed=-1, right_speed=-1, duration=0.3)
            self.drive(left_speed=-1, right_speed=1, duration=0.4)

        # If only the left sensor is over the edge, turn to the right,
        # then drive straight backwards.
        elif self.left_edge_detected():
            print("Backing to right and turning around")
            self.drive(left_speed=-0.5, right_speed=0.5, duration=0.25)
            self.drive(left_speed=-1, right_speed=-1, duration=0.3)
            self.drive(left_speed=-1, right_speed=1, duration=0.4)

        # If only the right sensor is over the edge, turn to the left,
        # then drive straight backwards.
        elif self.right_edge_detected():
            print("Backing to left and turning around")
            self.drive(left_speed=0.5, right_speed=-0.5, duration=0.25)
            self.drive(left_speed=-1, right_speed=-1, duration=0.3)
            self.drive(left_speed=1, right_speed=-1, duration=0.4)

        # ******************************
        # 2. Scan for opponent and charge it!
        # ******************************

        # Check for opponent straight ahead
        charge_time = 0
        if self.opponent_in_range_right() and self.opponent_in_range_left():
            # Charge!
            print("Charging boldly forward")
            charge_start_time = time.monotonic()
            self.drive(right_speed=MAX_SPEED, left_speed=MAX_SPEED)
            while (
                    self.opponent_in_range_right()
                    and self.opponent_in_range_left()
                    and not (self.right_edge_detected() or self.left_edge_detected())
                    and time.monotonic() - charge_start_time < MAX_CHARGE_TIME
            ):
                sleep(CHARGE_INTERVAL)
                charge_time += CHARGE_INTERVAL
            self.stop()
            if time.monotonic() - charge_start_time >= MAX_CHARGE_TIME:
                print("Backing up and turning away from opponent")
                if random.randint(0, 1):
                    self.drive(left_speed=-0.7, right_speed=-0.3, duration=BACK_AWAY_TIME)
                else:
                    self.drive(left_speed=-0.3, right_speed=-0.7, duration=BACK_AWAY_TIME)
        # Check for opponent to right
        else:
            right_distance = self.right_distance()
            left_distance = self.left_distance()
            if right_distance < MAX_DISTANCE:
                print("Looking right")
                # Turn to the right - set turn duration inversely proportional to opponent distance
                self.drive(left_speed=TURN_SPEED, right_speed=-TURN_SPEED, duration=0.2*((MAX_DISTANCE-right_distance)/MAX_DISTANCE))

            # Check for opponent to left
            elif left_distance < MAX_DISTANCE:
                print("Looking left")
                # Turn to the left - set turn duration inversely proportional to opponent distance
                self.drive(left_speed=-TURN_SPEED, right_speed=TURN_SPEED, duration=0.2*((MAX_DISTANCE-left_distance)/MAX_DISTANCE))

            # Spin and look for opponent
            else:
                # Turn to the left or right
                print("Spinning")
                if self.spin_right:
                    self.drive(left_speed=-TURN_SPEED, right_speed=TURN_SPEED, duration=TURN_DURATION)
                else:
                    self.drive(left_speed=TURN_SPEED, right_speed=-TURN_SPEED, duration=TURN_DURATION)

if __name__ == "__main__":
    SimpleSumoBot().run()

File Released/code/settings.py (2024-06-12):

import board


################################################################
# Settings that control fight mode parameters
# Adjusting these values is an easy way to change your strategy.
################################################################

# Maximum enemy targeting range
MAX_DISTANCE = 600

# Time to charge forward before checking sensors
CHARGE_INTERVAL = 0.05

# Maximum number of seconds to charge before assuming stalemate
MAX_CHARGE_TIME = 5

# Number of seconds to back away from opponent when stalemate detected
BACK_AWAY_TIME = 2

# Maximum charging speed (0-1)
MAX_SPEED = 0.7

# Turning speed (0-1)
TURN_SPEED = 0.5

# Turning duration in seconds when searching for opponent
TURN_DURATION = 0.05


##################################################
# Robot hardware settings
# Change these if your robot is wired differently
# than the instructions, you renegade.
##################################################

# Pin connected to piezo buzzer
PIEZO_PIN = board.GP22

# Pins connected to DC motors (swap variable names if your motors are connected differently)
RIGHT_MOTOR_PIN_B = board.GP11
RIGHT_MOTOR_PIN_A = board.GP10
LEFT_MOTOR_PIN_A = board.GP8
LEFT_MOTOR_PIN_B = board.GP9

# Pin connected to NeoPixels
NEO_PIXEL_PIN = board.GP18

# Pins connected to buttons
BUTTON_1_PIN = board.GP20
BUTTON_2_PIN = board.GP21

# Pins connected to TOF sensors
LEFT_EDGE_SENSOR_PIN = board.GP5
RIGHT_EDGE_SENSOR_PIN = board.GP26
TOF_LEFT_I2C_PINS = (board.GP17, board.GP16)
TOF_RIGHT_I2C_PINS = (board.GP3, board.GP2)
I2C_LEFT_TOGGLE_PIN = board.GP4
I2C_RIGHT_TOGGLE_PIN = board.GP6

# Pin for battery voltage reference path
BATTERY_VOLTAGE_PIN = board.A3
# Low battery threshold voltage
BATTERY_VOLTAGE_THRESHOLD = 52500

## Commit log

2024-01-24 da
    da
    [1x4 AA battery holder.stl, 2x2 AA battery holder.stl, K345-wheel-42x19mm lowres.stl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]
2024-01-30 do
    do
    [wheelmotormount assembly.stl]
2024-02-07 TOF sensor working
2024-02-14 For Bill Ball sumo bot design 4
    see https://www.tinkercad.com/things/8du6Ch6ZOo7-public-sumo-bot-4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 for assembly tips
    [battery holder bridge.stl, blade.stl, left fender.stl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]
2024-02-14 Create code.py
    A simple script for testing. Pin assignments are in comments at the end of the file
2024-02-16 Basic fighting routine with TOF and edge sensors
2024-02-21 Refactor folder name
    [battery holder bridge.stl, blade.stl, left fender.stl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]
2024-03-12 BB1 files
    [Sumo BB1 blade.stl, Sumo BB1 body.stl, Sumo BB1 fender bar.stl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]
2024-03-17 Refactor robot state logic, add low battery alert logic
2024-04-23 updates
    updates
    [1x4 AA battery holder.stl, 2x2 AA battery holder.stl, K345-wheel-42x19mm lowres.stl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]
2024-05-18 Update Sumo BB1 fender bar.stl
    [Sumo BB1 fender bar.stl]
2024-06-12 Update settings.py
    fixed turn_duration
    [settings.py]
2024-06-20 Fix bug that kept bot from spinning correctly
    [base_bot.py, code.py]
2024-06-24 Holder for servo stl file
    [SumoBot Accessory Holder v1 v3.stl]
